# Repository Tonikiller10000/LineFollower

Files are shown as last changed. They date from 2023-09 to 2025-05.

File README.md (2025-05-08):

# LineFollower V5.0

## Description:

<table>
  <tr>
    <td>
    This is an robot made to follow a black line from start to finish for various competitions. 
    
It uses:
- ATmega328p-AU as an microcontroller(used in arduino uno);
- 16 or 20Mhz crystal resonator;
- [TB6612FNG](https://github.com/Tonikiller10000/MotorDriver_1) DC motor driver;
- [ITR8307-TR8](https://github.com/Tonikiller10000/ITR8307-TR8_SensorBar) sensor bar;
- LI-PO battery (7.2V)
- 2x DC motors with low torque high speed gear box
- robot suport (Wood, 3d printed or any low weight matherial)
    </td>
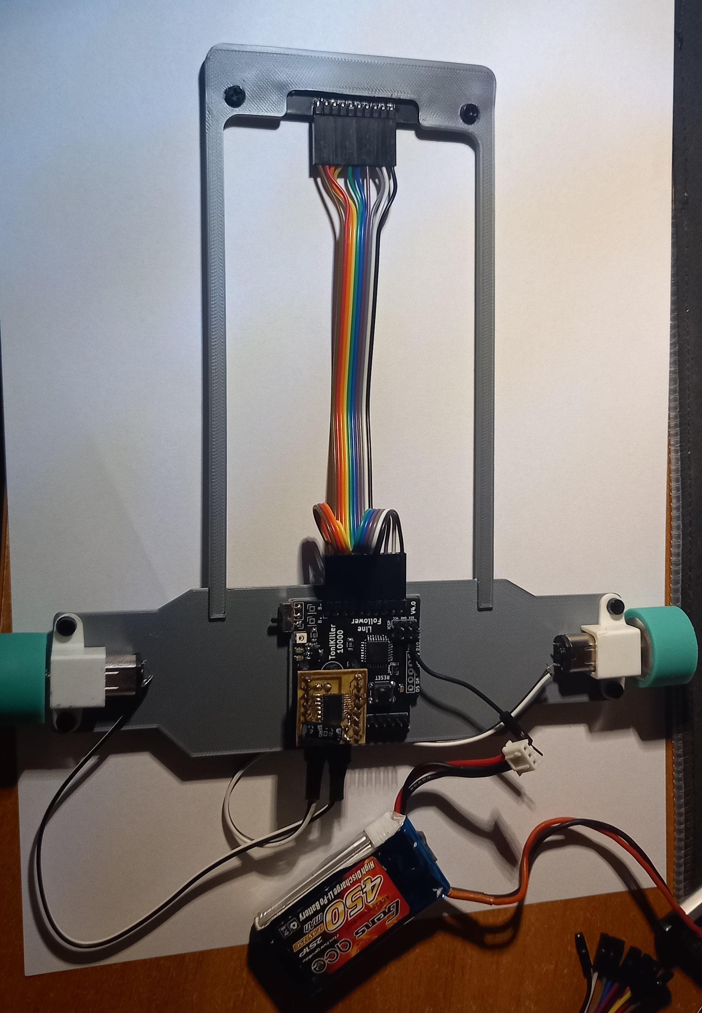
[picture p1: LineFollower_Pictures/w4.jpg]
    <td></td>
  </tr>
</table>

 ## LineFollower V5.0
<table>
  <tr>
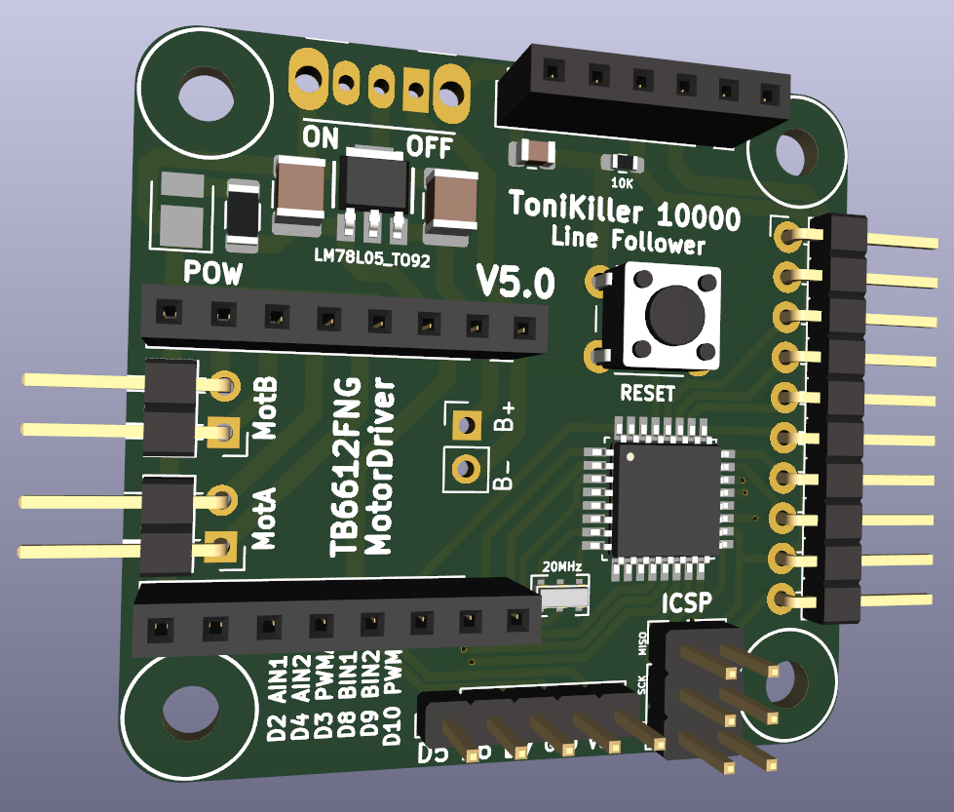
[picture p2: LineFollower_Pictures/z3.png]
    <td></td>
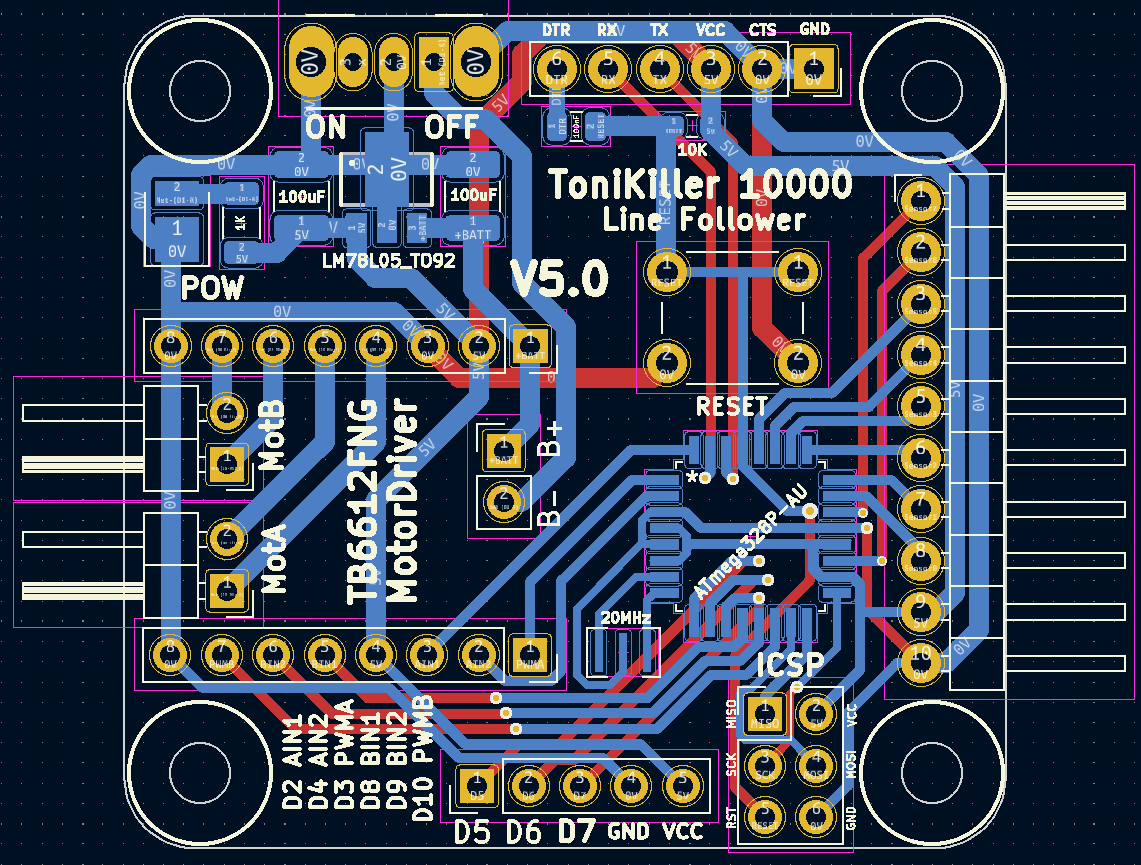
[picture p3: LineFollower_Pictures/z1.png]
    <td></td>
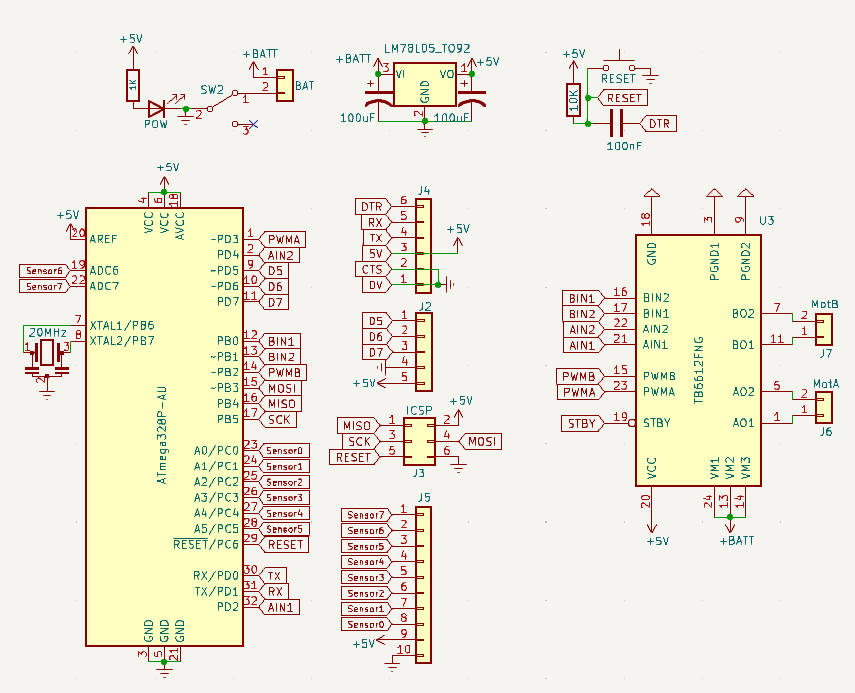
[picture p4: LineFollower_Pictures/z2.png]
    <td></td>
  </tr>
</table>

 ## LineFollower V4.0(old design)
<table>
  <tr>
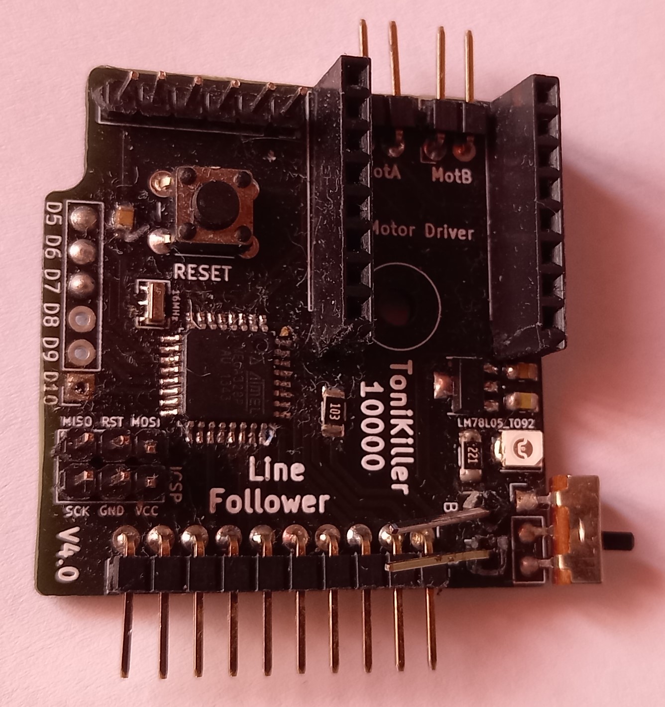
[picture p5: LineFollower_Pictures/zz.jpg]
    <td></td>
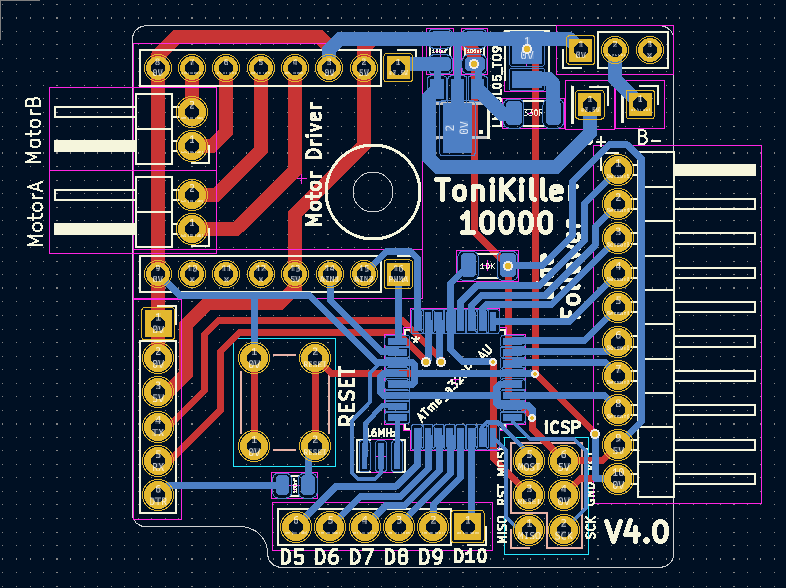
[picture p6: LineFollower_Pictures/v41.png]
    <td></td>
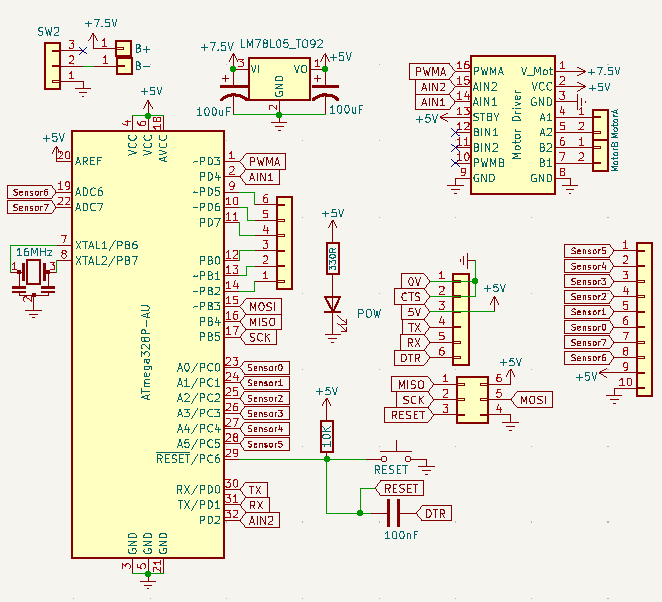
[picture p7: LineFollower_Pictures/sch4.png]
    <td></td>
  </tr>
</table>

### How it works:
The board is like a custom arduino UNO board powered from an 7.2V Li-Po battery trouth an 5V voltage regulator. The 8 analog pins are used as inputs from the sensor bar and 6 digital pins are used for the TB6612FNG motor driver witch is powered dirrectly from the battery to give more power to the motors. The reset pin has a 10K pullup resistor witch is pulled down by the reset button when it is pressed. The UART and ICSP pins wore pulled out to program the code and the bootloader of the IC.

### Programming:
[Programming of the robot](https://github.com/Tonikiller10000/LineFollower/blob/main/LineFollower_Pictures/w6.jpg): is done via UART protocoll with an [FTDI](https://github.com/Tonikiller10000/CH340G-FTDI-PROGRAMER) programming board. The code for the LineFollower is not ready. It uses the PID algorithm, and further documentation about this algorithm and the  source code for the robot will be posted this year.

### Start remote:

Robochalange remote:
[Start switch website](https://p1r.se/startmodule/)
[Start switch github](https://github.com/p1rse/robot-sumo-start-module/)
[IR Receiver Diode - TSOP38238](https://www.sparkfun.com/products/10266)
[schematic1](https://blogger.googleusercontent.com/img/b/R29vZ2xl/AVvXsEgnkNo1QEsxSPMNj7rN0opPGzlpkEMgxas9PnXUh-xvVR3l7UK27BbSvRroJmsxzwf3StBiDH0k4m-aEXX_4qJKeG5T4bKsfCBbcjgoykJY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)
[schematic2](https://blogger.googleusercontent.com/img/b/R29vZ2xl/AVvXsEjLlN9CDAmP0rq2BlWM0Xdsypyy7NfGZpMYkufZPUAMmgCRdU-KhBC8AvPr7iOOQAwod2Hw66K_vuib1FNqDIHNemtnMvlSue2krN2hfp39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)
[Q&A](https://robochallenge.ro/faq)
[MORE](https://destroyer3000.blogspot.com/2013/03/start-module-implement-yourself.html)

### How PID control work/`s

[Here](https://www.youtube.com/playlist?list=PLn8PRpmsu08pQBgjxYFXSsODEF3Jqmm-y) you can learn more about PID and under this you can see 
an analog linefollower project with and without PID:
- https://www.nutsvolts.com/magazine/article/the_pid_controller_part_1
- https://www.ecircuitcenter.com/Circuits/op_pid/op_pid.htm
- https://control.com/textbook/closed-loop-control/analog-electronic-pid-controllers/
- https://www.youtube.com/watch?v=4Y7zG48uHRo&list=PLOSOqCeZCHL0Qxb6YyrvGzjCg9FLfzHYJ

### ///////////////////////////////
- Small linefollower with op amp:https://www.youtube.com/watch?v=zZmvL0TkllI&list=WL&index=15&t=25s

### Design and mentions
[Robot support design considerations](https://github.com/Tonikiller10000/LineFollower/blob/main/LineFollower_Pictures/w3.png):
- to reach lower inertia, the components and the most of the mass of the robot should be placed on it\`s back;
- to reach a longer allowed response time from the sensor line detection to the mottor speed change it should be builted longer;
- to reach better torque on the wheels, it should be wider. 
- to mount the motors use molderd plastic motor holders, or be carefull when printing [it](https://github.com/Tonikiller10000/LineFollower/blob/main/LineFollower_Pictures/w1.jpg). 
- the case was made with autodesk fusion 360 at the 3d printer and with some M3 screws.

The next version will have the motor driver soldered on the board and motors screwed dirrectly to it as the suport. 
Another version will have a turbine for better torque and faster speeds.

## Links: 
- ATmega328p-AU (microcontroller): 
- LM78L05 (5V voltage regulator):
- Proof of work: https://github.com/Tonikiller10000/LineFollower/blob/main/LineFollower_Pictures/w2.mp4

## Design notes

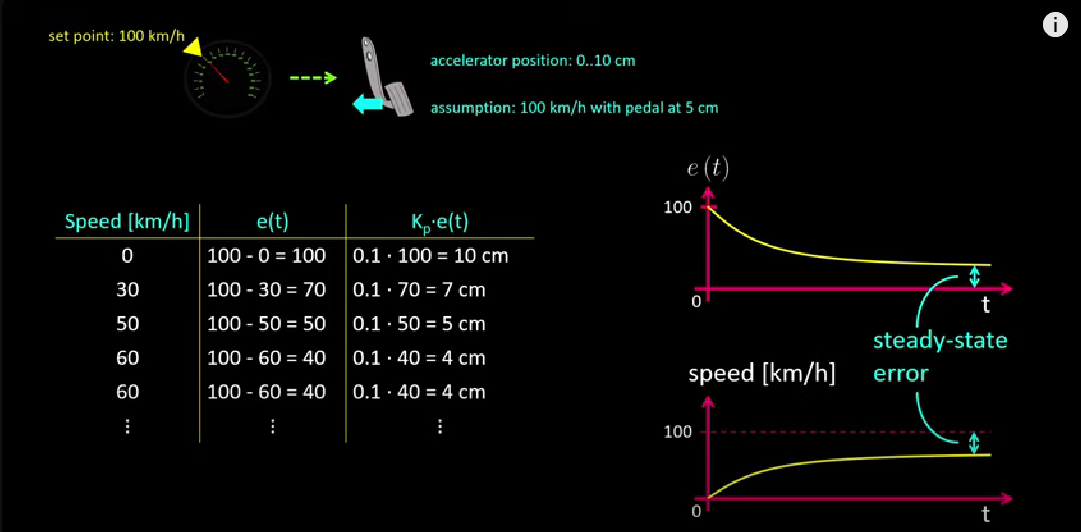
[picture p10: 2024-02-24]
PID SOFT ROBOT/Screenshot 2023-11-08 183037.png

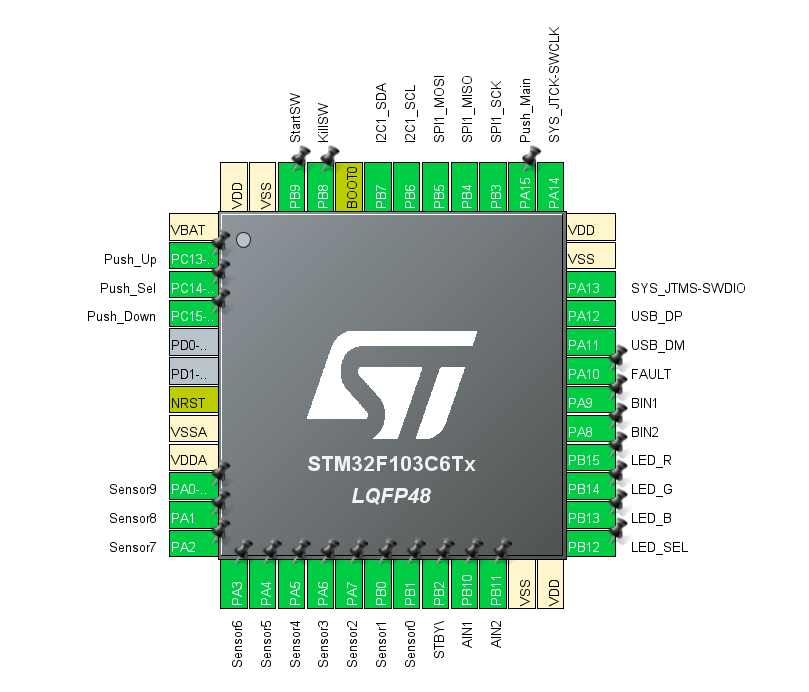
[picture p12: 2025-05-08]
LineFollower_Pictures/V6/LineFollower (17).png

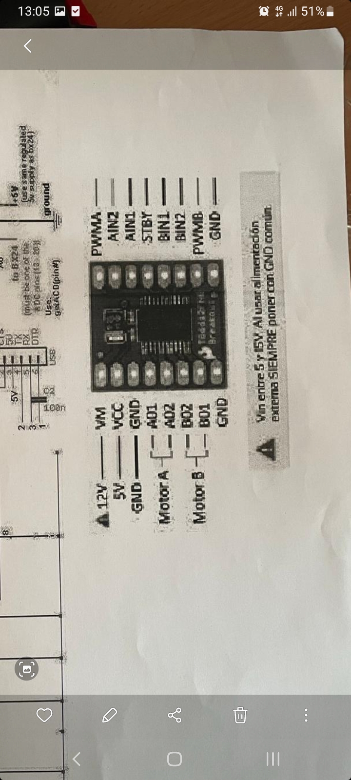
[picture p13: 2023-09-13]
LineFollower_Pictures/Screenshot_20230825-130534_Gallery.jpg

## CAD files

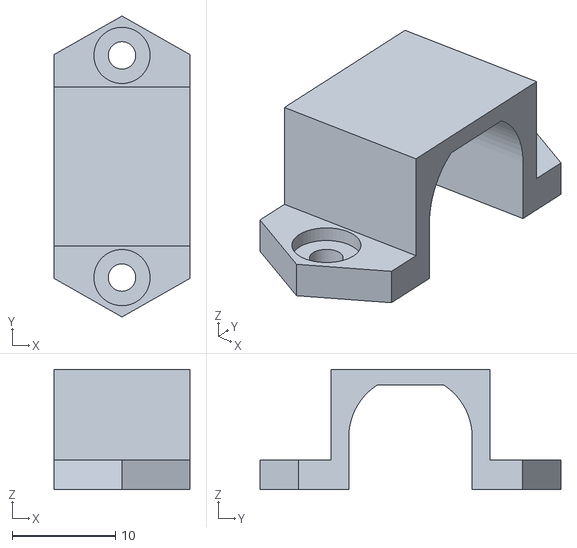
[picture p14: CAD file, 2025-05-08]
LineFollower_V6.0/n20_fixation.STL
13.1 x 29.1 x 11.6

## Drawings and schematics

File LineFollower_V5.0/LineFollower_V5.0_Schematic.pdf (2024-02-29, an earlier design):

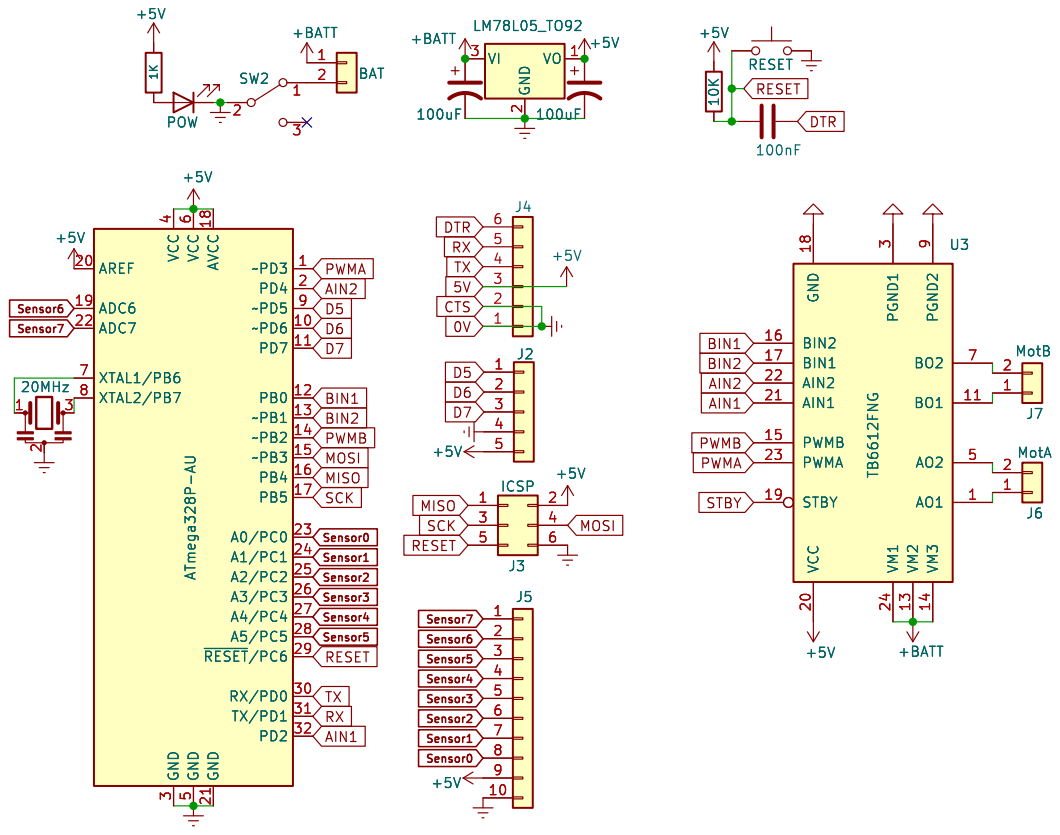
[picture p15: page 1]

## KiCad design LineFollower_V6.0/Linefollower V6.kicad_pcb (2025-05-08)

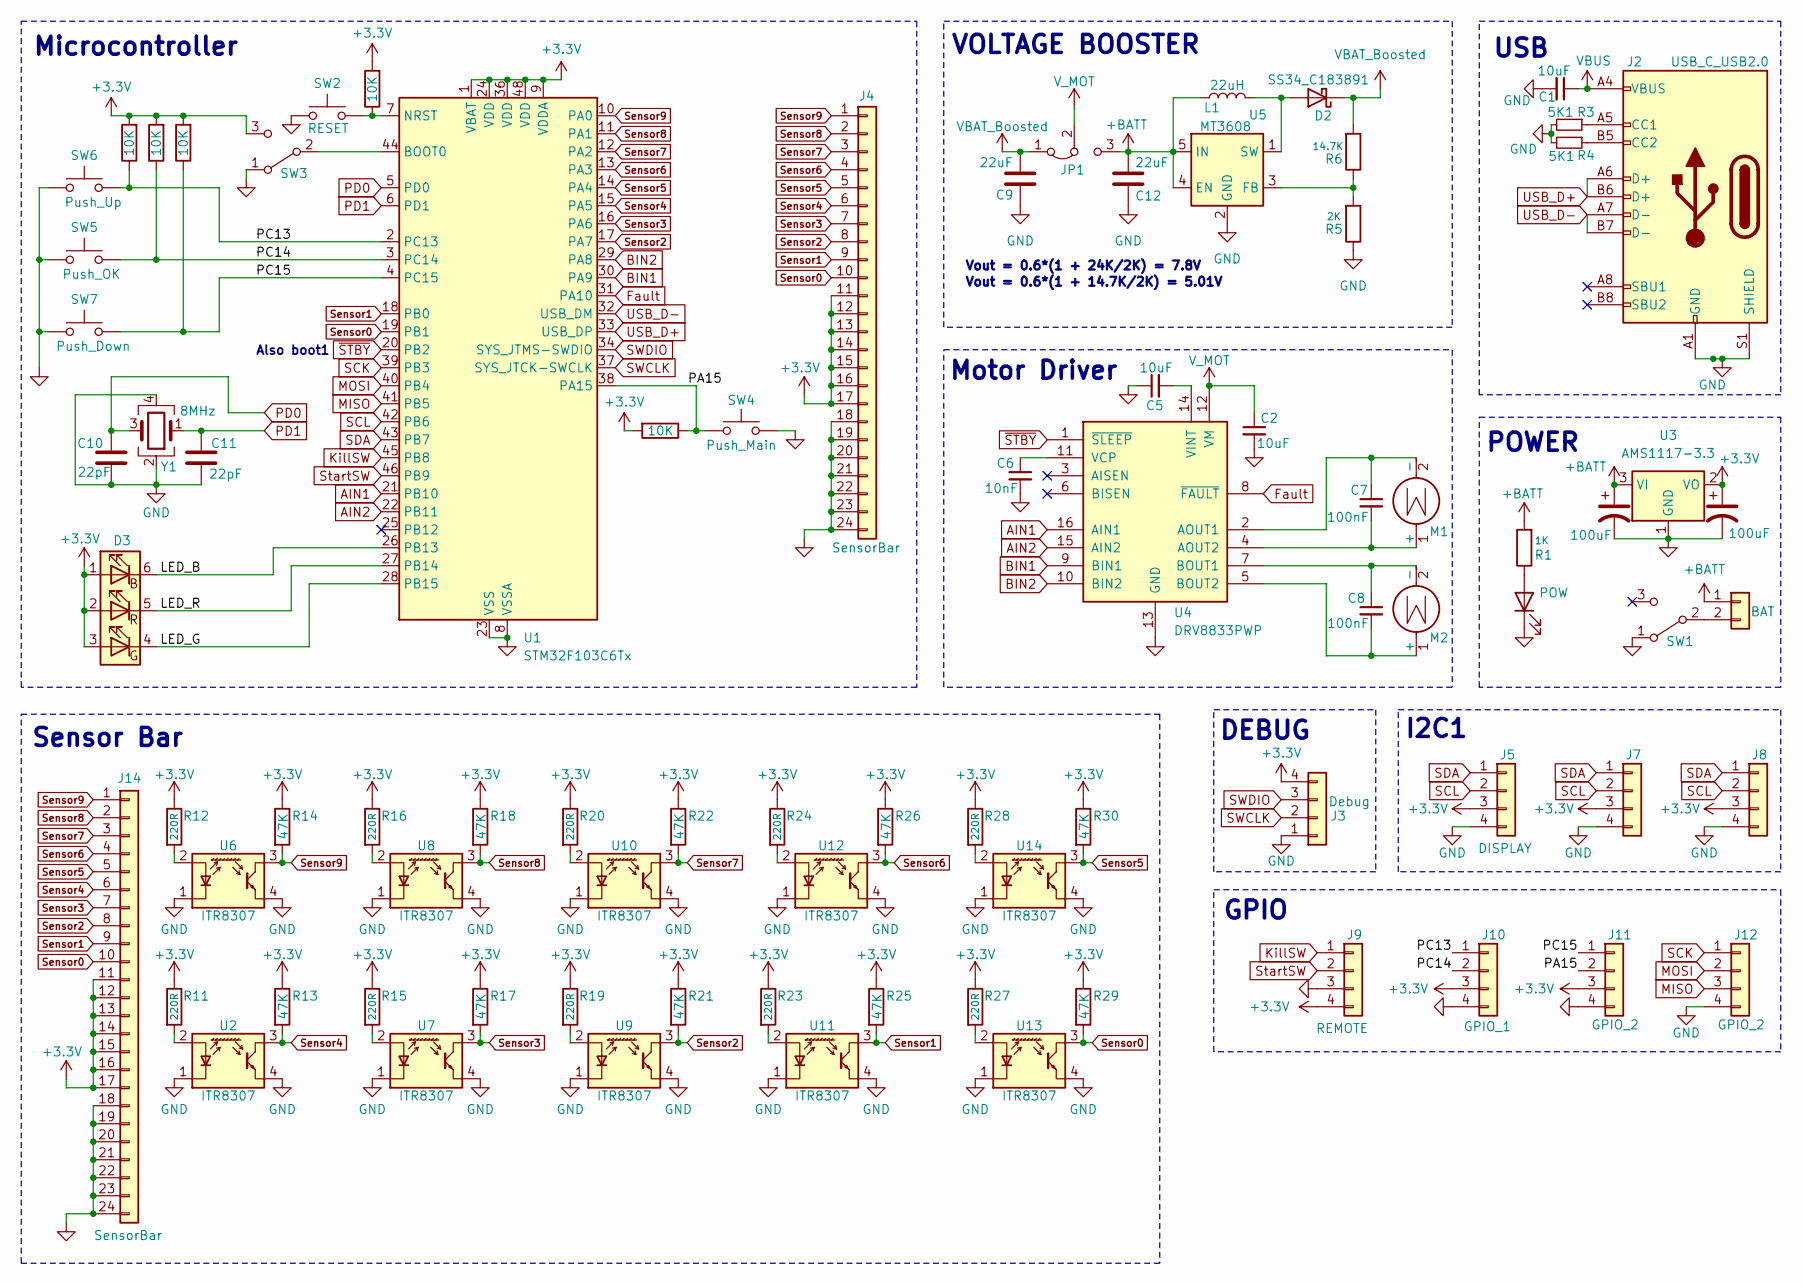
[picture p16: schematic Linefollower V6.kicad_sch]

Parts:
C1, C2, C5: 10uF; C_0603_1608Metric
C3, C4: 100uF; C_1210_3225Metric_Pad1.33x2.70mm_HandSolder
C6: 10nF; C_0603_1608Metric
C7, C8: 100nF; C_0603_1608Metric
C9, C12: 22uF
C10, C11: 22pF
D1: POW
D2: SS34_C183891
D3: SMLVN6RGB; LED_ROHM_SMLVN6
J1: BAT; PinHeader_1x02_P2.54mm_Vertical
J2: USB_C_USB2.0
J3: Debug; PinHeader_1x04_P2.54mm_Horizontal
J4, J14: SensorBar
J5, J7, J8: DISPLAY; PinHeader_1x04_P2.54mm_Vertical
J9: REMOTE; PinHeader_1x04_P2.54mm_Vertical
J10: GPIO_1; PinHeader_1x04_P2.54mm_Vertical
J11, J12: GPIO_2; PinHeader_1x04_P2.54mm_Vertical
JP1: Jumper_3_Bridged12
L1: 22uH; L_7.3x7.3_H4.5
M1, M2: Motor_DC; PinHeader_1x02_P2.54mm_Vertical
R1: 1K; R_1206_3216Metric
R2, R7, R8, R9, R10: 10K; R_1206_3216Metric
R3, R4: 5K1; R_0603_1608Metric
R5: 2K; R_0805_2012Metric_Pad1.20x1.40mm_HandSolder
R6: 14.7K; R_0805_2012Metric_Pad1.20x1.40mm_HandSolder
R11, R12, R15, R16, R19, R20, R23, R24, R27, R28: 220R; R_1206_3216Metric_Pad1.30x1.75mm_HandSolder
R13, R14, R17, R18, R21, R22, R25, R26, R29, R30: 47K; R_1206_3216Metric_Pad1.30x1.75mm_HandSolder
SW1, SW3: SW_SPDT
SW2: RESET
SW4: Push_Main
SW5: Push_OK
SW6: Push_Up
SW7: Push_Down
U1: STM32F103C6Tx; LQFP-48_7x7mm_P0.5mm
U2, U6, U7, U8, U9, U10, U11, U12, U13, U14: ITR8307; Everlight_ITR8307
U3: AMS1117-3.3; SOT-223-3_TabPin2
U4: DRV8833PWP; HTSSOP-16-1EP_4.4x5mm_P0.65mm_EP3.4x5mm_Mask2.46x2.31mm_The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
U5: MT3608; SOT-23-6
Y1: 8MHz

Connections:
+3.3V: C4.1, D3.1 (BA), D3.2 (RA), D3.3 (GA), J3.4, J4.11, J4.12, J4.13, J4.14, J4.15, J4.16, J4.17, J5.3, J7.3, J8.3, J9.4, J10.3, J11.3, J14.11, J14.12, J14.13, J14.14, J14.15, J14.16, J14.17, R2.2, R7.2, R8.2, R9.2, R10.2, R11.1, R12.1, R13.1, R14.1, R15.1, R16.1, R17.1, R18.1, R19.1, R20.1, R21.1, R22.1, R23.1, R24.1, R25.1, R26.1, R27.1, R28.1, R29.1, R30.1, SW3.3 (C), U1.1 (VBAT), U1.9 (VDDA), U1.24 (VDD), U1.36 (VDD), U1.48 (VDD), U3.2 (VO)
+BATT: C3.1, C12.1, J1.1, JP1.3 (B), L1.1, R1.2, U3.3 (VI), U5.4 (EN), U5.5 (IN)
/LED_B: D3.6 (BK), U1.26 (PB13)
/LED_G: D3.4 (GK), U1.28 (PB15)
/LED_R: D3.5 (RK), U1.27 (PB14)
/PA15: J11.2, R10.1, SW4.1, U1.38 (PA15)
/PC13: J10.1, R7.1, SW6.2, U1.2 (PC13)
/PC14: J10.2, R8.1, SW5.2, U1.3 (PC14)
/PC15: J11.1, R9.1, SW7.2, U1.4 (PC15)
AIN1: U1.21 (PB10), U4.16 (AIN1)
AIN2: U1.22 (PB11), U4.15 (AIN2)
BIN1: U1.30 (PA9), U4.9 (BIN1)
BIN2: U1.29 (PA8), U4.10 (BIN2)
Fault: U1.31 (PA10), U4.8 (~FAULT)
GND: C1.2, C2.2, C3.2, C4.2, C5.1, C6.2, C9.1, C10.1, C11.1, C12.2, D1.1 (K), J2.A1 (GND), J2.B1 (GND), J2.S1 (SHIELD), J3.1, J4.18, J4.19, J4.20, J4.21, J4.22, J4.23, J4.24, J5.4, J7.4, J8.4, J9.3, J10.4, J11.4, J12.4, J14.18, J14.19, J14.20, J14.21, J14.22, J14.23, J14.24, R3.2, R4.2, R5.1, SW1.1 (A), SW2.2, SW3.1 (A), SW4.2, SW5.1, SW6.1, SW7.1, U1.8 (VSSA), U1.23 (VSS), U1.35 (VSS), U1.47 (VSS), U2.1 (K), U2.4 (E), U3.1 (GND), U4.13 (GND), U4.17 (GND), U5.2 (GND), U6.1 (K), U6.4 (E), U7.1 (K), U7.4 (E), U8.1 (K), U8.4 (E), U9.1 (K), U9.4 (E), U10.1 (K), U10.4 (E), U11.1 (K), U11.4 (E), U12.1 (K), U12.4 (E), U13.1 (K), U13.4 (E), U14.1 (K), U14.4 (E), Y1.2, Y1.4; also elsewhere on the board
KillSW: J9.1, U1.45 (PB8)
MISO: J12.3, U1.41 (PB5)
MOSI: J12.2, U1.40 (PB4)
unnamed: D1.2 (A), R1.1
unnamed: D2.2 (A), L1.2, U5.1 (SW)
unnamed: J1.2, SW1.2 (B)
unnamed: J2.A5 (CC1), R3.1
unnamed: J2.B5 (CC2), R4.1
unnamed: C7.2, M1.1 (+), U4.4 (AOUT2)
unnamed: C7.1, M1.2 (-), U4.2 (AOUT1)
unnamed: C8.2, M2.1 (+), U4.5 (BOUT2)
unnamed: C8.1, M2.2 (-), U4.7 (BOUT1)
unnamed: SW3.2 (B), U1.44 (BOOT0)
unnamed: R2.1, SW2.1, U1.7 (NRST)
unnamed: R11.2, U2.2 (A)
unnamed: C6.1, U4.11 (VCP)
unnamed: C5.2, U4.14 (VINT)
unnamed: R5.2, R6.1, U5.3 (FB)
unnamed: R12.2, U6.2 (A)
unnamed: R15.2, U7.2 (A)
unnamed: R16.2, U8.2 (A)
unnamed: R19.2, U9.2 (A)
unnamed: R20.2, U10.2 (A)
unnamed: R23.2, U11.2 (A)
unnamed: R24.2, U12.2 (A)
unnamed: R27.2, U13.2 (A)
unnamed: R28.2, U14.2 (A)
PD0: C10.2, U1.5 (PD0), Y1.3; also elsewhere on the board
PD1: C11.2, U1.6 (PD1), Y1.1; also elsewhere on the board
SCK: J12.1, U1.39 (PB3)
SCL: J5.2, J7.2, J8.2, U1.42 (PB6)
SDA: J5.1, J7.1, J8.1, U1.43 (PB7)
SWCLK: J3.2, U1.37 (SYS_JTCK-SWCLK)
SWDIO: J3.3, U1.34 (SYS_JTMS-SWDIO)
Sensor0: J4.10, J14.10, R29.2, U1.19 (PB1), U13.3 (C)
Sensor1: J4.9, J14.9, R25.2, U1.18 (PB0), U11.3 (C)
Sensor2: J4.8, J14.8, R21.2, U1.17 (PA7), U9.3 (C)
Sensor3: J4.7, J14.7, R17.2, U1.16 (PA6), U7.3 (C)
Sensor4: J4.6, J14.6, R13.2, U1.15 (PA5), U2.3 (C)
Sensor5: J4.5, J14.5, R30.2, U1.14 (PA4), U14.3 (C)
Sensor6: J4.4, J14.4, R26.2, U1.13 (PA3), U12.3 (C)
Sensor7: J4.3, J14.3, R22.2, U1.12 (PA2), U10.3 (C)
Sensor8: J4.2, J14.2, R18.2, U1.11 (PA1), U8.3 (C)
Sensor9: J4.1, J14.1, R14.2, U1.10 (PA0), U6.3 (C)
StartSW: J9.2, U1.46 (PB9)
USB_D+: J2.A6 (D+), J2.B6 (D+), U1.33 (USB_DP)
USB_D-: J2.A7 (D-), J2.B7 (D-), U1.32 (USB_DM)
VBAT_Boosted: C9.2, D2.1 (K), JP1.1 (A), R6.2
VBUS: C1.1, J2.A4 (VBUS)
V_MOT: C2.1, JP1.2 (C), U4.12 (VM)
~STBY: U1.20 (PB2), U4.1 (~SLEEP)

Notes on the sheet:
Motor Driver
Also boot1
Vout = 0.6*(1 + 24K/2K) = 7.8V
POWER
Sensor Bar
Microcontroller
I2C1
USB
VOLTAGE BOOSTER
GPIO
Vout = 0.6*(1 + 14.7K/2K) = 5.01V
DEBUG

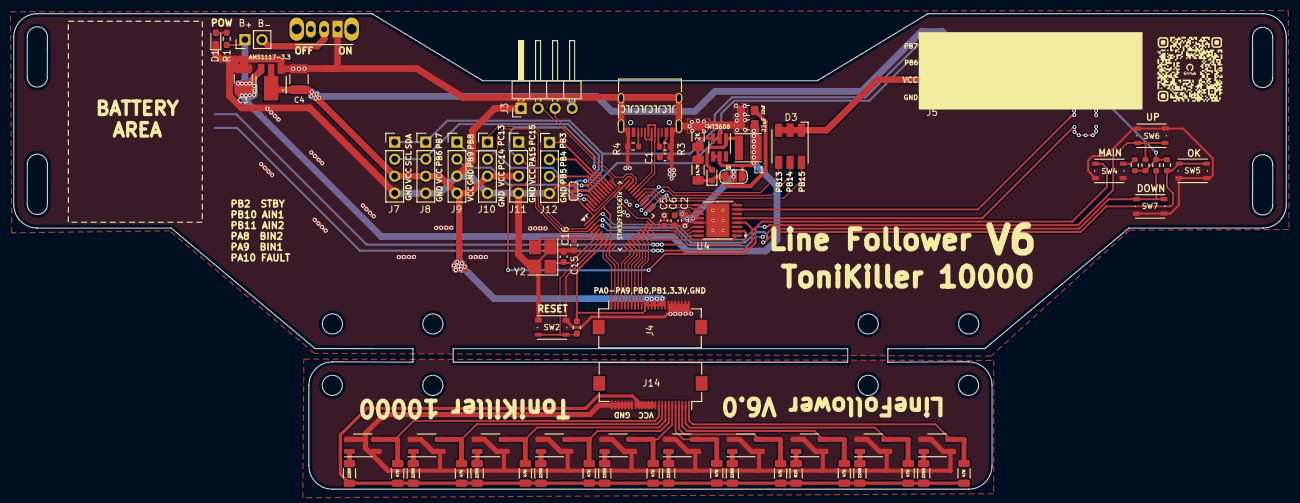
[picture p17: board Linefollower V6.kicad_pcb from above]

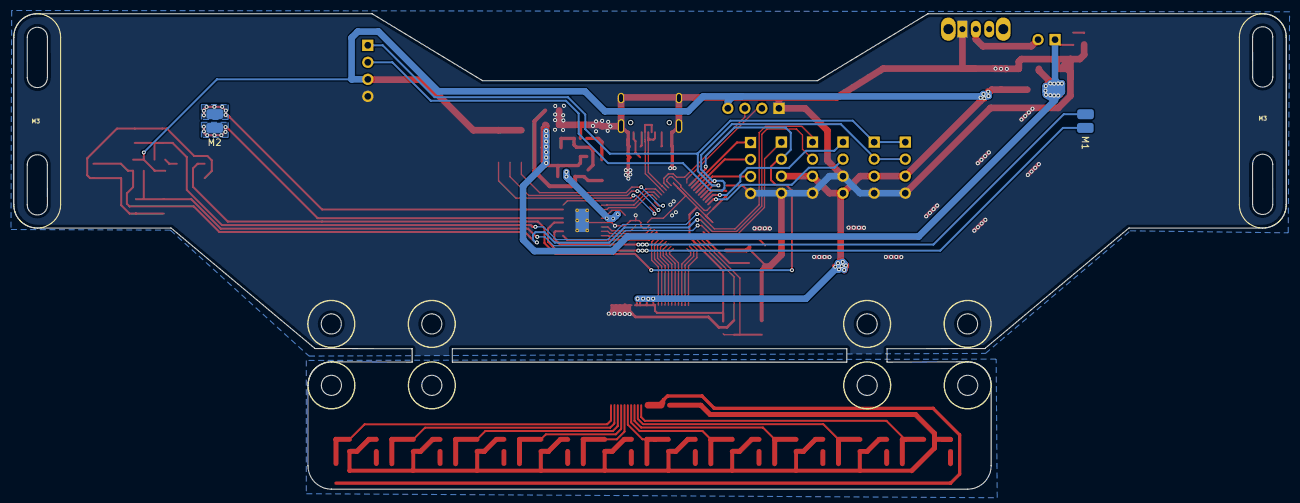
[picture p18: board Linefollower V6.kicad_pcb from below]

Board: 2 copper layers, 190.0 x 71.0 mm, 81 parts (2 on the bottom side), 66 nets.

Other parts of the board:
C15, C16: 22pF; C_0603_1608Metric
Y2: 8MHz; Crystal_SMD_3225-4Pin_3.2x2.5mm_HandSoldering

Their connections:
GND: C15.1, C16.1, Y2.2, Y2.4; also elsewhere on the board
PD0: C15.2, Y2.3; also elsewhere on the board
PD1: C16.2, Y2.1; also elsewhere on the board

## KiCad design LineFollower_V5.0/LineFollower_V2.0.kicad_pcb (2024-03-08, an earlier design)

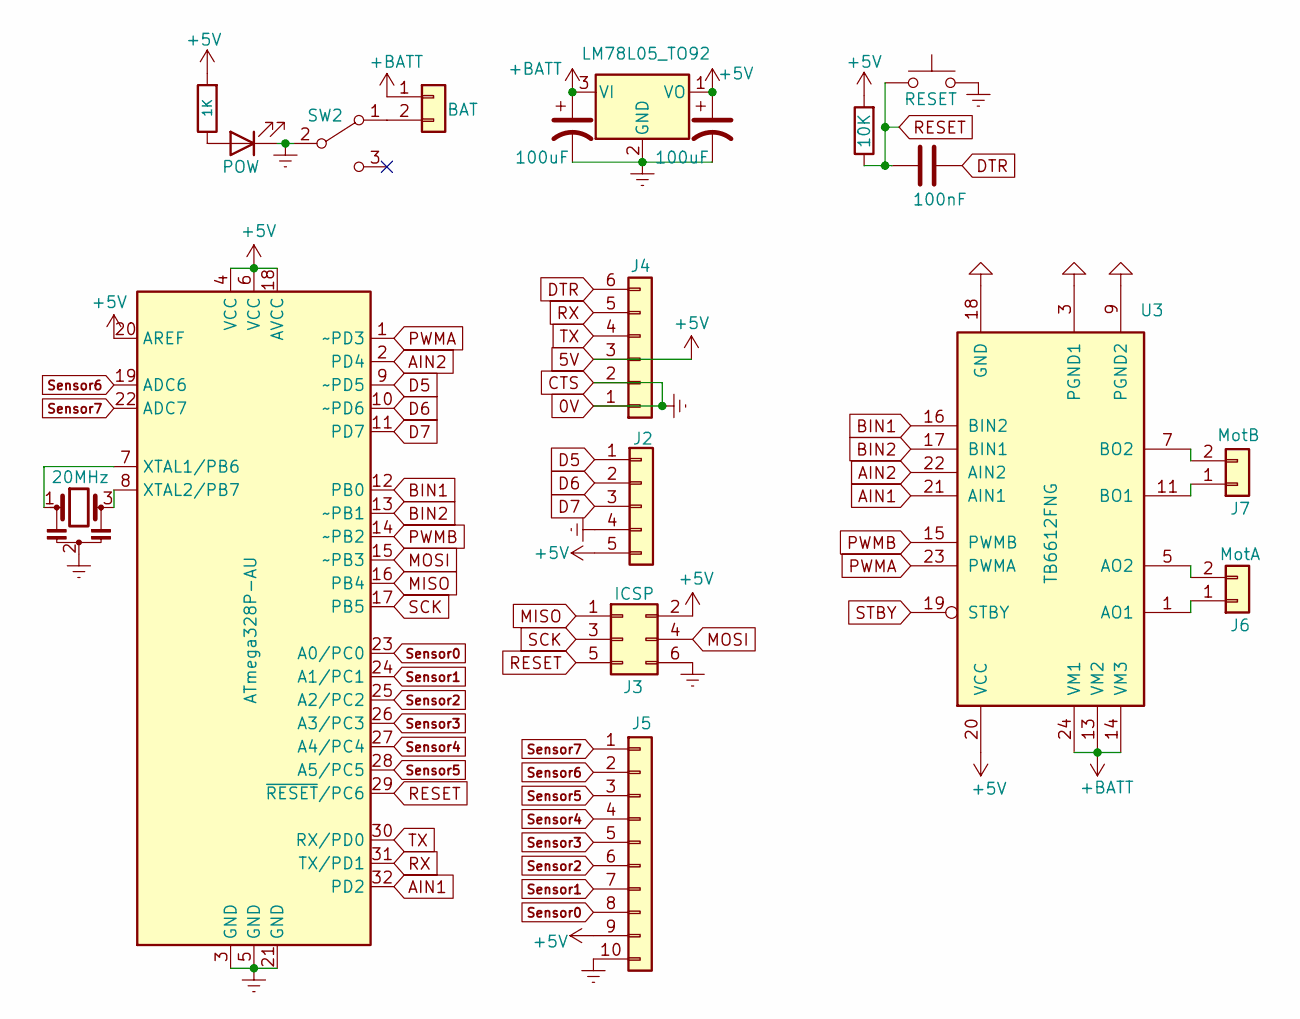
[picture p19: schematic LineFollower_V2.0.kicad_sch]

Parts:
C2, C3: 100uF; C_1210_3225Metric_Pad1.33x2.70mm_HandSolder
C6: 100nF; C_0805_2012Metric
D1: POW
J1: BAT; PinHeader_1x02_P2.54mm_Vertical
J2: Conn_01x05
J3: ICSP; PinHeader_2x03_P2.54mm_Vertical
J4: Conn_01x06_MountingPin
J5: Conn_01x10; PinHeader_1x10_P2.54mm_Horizontal
J6: MotA; PinHeader_1x02_P2.54mm_Vertical
J7: MotB; PinHeader_1x02_P2.54mm_Vertical
R1: 10K; R_1206_3216Metric
R2: 1K; R_1206_3216Metric
SW1: RESET
SW2: SW_SPDT
U1: ATmega328P-AU; TQFP-32_7x7mm_P0.8mm
U2: LM78L05_TO92; TO-92_Inline
U3: TB6612FNG; SSOP-24_5.3x8.2mm_P0.65mm
Y1: 20MHz; Resonator_SMD_Murata_CSTxExxV-3Pin_3.0x1.1mm

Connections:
0V: C2.2, C3.2, D1.1 (K), J2.4, J3.6, J4.1, J4.2, J5.10, SW1.2, SW2.2 (B), U1.3 (GND), U1.5 (GND), U1.21 (GND), U2.2 (GND), Y1.2; also elsewhere on the board
5V: C3.1, J2.5, J3.2, J4.3, J5.9, R1.2, R2.2, U1.4 (VCC), U1.6 (VCC), U1.18 (AVCC), U1.20 (AREF), U2.1 (VO), U3.20 (VCC); also elsewhere on the board
+BATT: C2.1, J1.1, U2.3 (VI), U3.13 (VM2), U3.14 (VM3), U3.24 (VM1); also elsewhere on the board
AIN1: U1.32 (PD2), U3.21 (AIN1); also elsewhere on the board
AIN2: U1.2 (PD4), U3.22 (AIN2); also elsewhere on the board
BIN1: U1.12 (PB0), U3.16 (BIN2); also elsewhere on the board
BIN2: U1.13 (~PB1), U3.17 (BIN1); also elsewhere on the board
D5: J2.1, U1.9 (~PD5)
D6: J2.2, U1.10 (~PD6)
D7: J2.3, U1.11 (PD7)
DTR: C6.1, J4.6
MISO: J3.1, U1.16 (PB4)
MOSI: J3.4, U1.15 (~PB3)
unnamed: D1.2 (A), R2.1
unnamed: J1.2, SW2.1 (A)
unnamed 15: J6.1, U3.1 (AO1), U3.2 (AO1); also elsewhere on the board
unnamed 16: J6.2, U3.5 (AO2), U3.6 (AO2); also elsewhere on the board
unnamed 17: J7.1, U3.11 (BO1), U3.12 (BO1); also elsewhere on the board
unnamed 18: J7.2, U3.7 (BO2), U3.8 (BO2); also elsewhere on the board
unnamed: U1.7 (XTAL1/PB6), Y1.1
unnamed: U1.8 (XTAL2/PB7), Y1.3
unnamed: U3.3 (PGND1), U3.4 (PGND1), U3.9 (PGND2), U3.10 (PGND2), U3.18 (GND)
PWMA: U1.1 (~PD3), U3.23 (PWMA); also elsewhere on the board
PWMB: U1.14 (~PB2), U3.15 (PWMB); also elsewhere on the board
RESET: C6.2, J3.5, R1.1, SW1.1, U1.29 (~RESET/PC6)
RX: J4.5, U1.31 (TX/PD1)
SCK: J3.3, U1.17 (PB5)
Sensor0: J5.8, U1.23 (A0/PC0)
Sensor1: J5.7, U1.24 (A1/PC1)
Sensor2: J5.6, U1.25 (A2/PC2)
Sensor3: J5.5, U1.26 (A3/PC3)
Sensor4: J5.4, U1.27 (A4/PC4)
Sensor5: J5.3, U1.28 (A5/PC5)
Sensor6: J5.2, U1.19 (ADC6)
Sensor7: J5.1, U1.22 (ADC7)
TX: J4.4, U1.30 (RX/PD0)

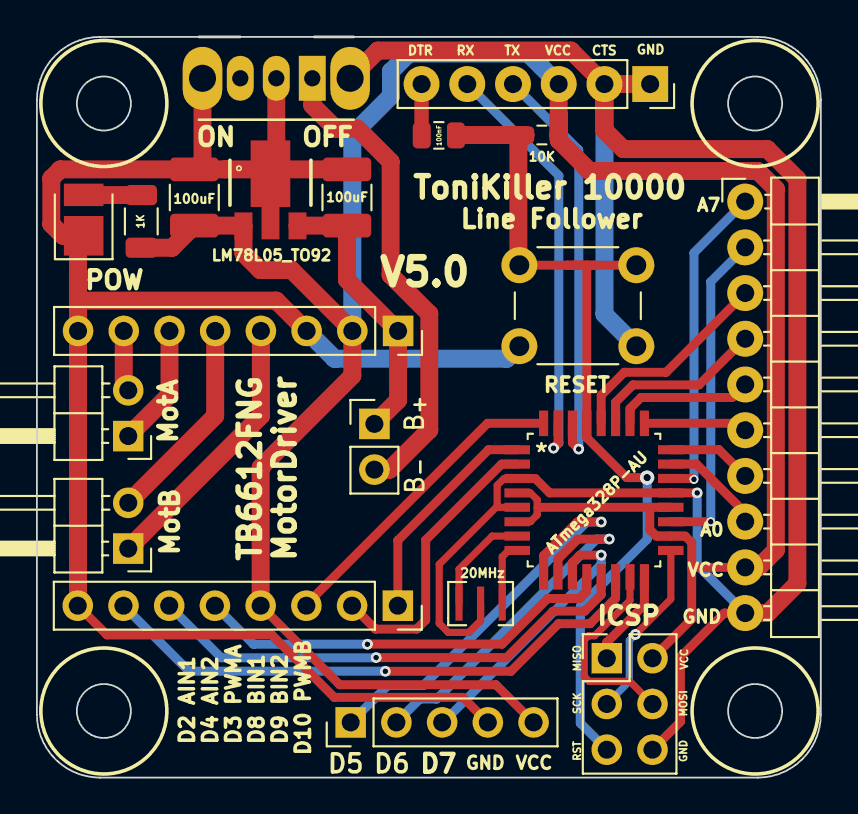
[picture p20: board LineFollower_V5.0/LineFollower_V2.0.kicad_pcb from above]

Board: 2 copper layers, 43.5 x 41.2 mm, 20 parts (0 on the bottom side), 35 nets.

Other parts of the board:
J8: BAT; PinSocket_1x08_P2.54mm_Vertical
J9: Conn_01x03; PinSocket_1x08_P2.54mm_Vertical

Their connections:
0V: J8.3, J8.8, J9.8; also elsewhere on the board
5V: J8.2, J9.4; also elsewhere on the board
+BATT: J8.1; also elsewhere on the board
AIN1: J9.3; also elsewhere on the board
AIN2: J9.2; also elsewhere on the board
BIN1: J9.5; also elsewhere on the board
BIN2: J9.6; also elsewhere on the board
unnamed 15: J8.6; also elsewhere on the board
unnamed 16: J8.7; also elsewhere on the board
unnamed 17: J8.4; also elsewhere on the board
unnamed 18: J8.5; also elsewhere on the board
PWMA: J9.1; also elsewhere on the board
PWMB: J9.7; also elsewhere on the board

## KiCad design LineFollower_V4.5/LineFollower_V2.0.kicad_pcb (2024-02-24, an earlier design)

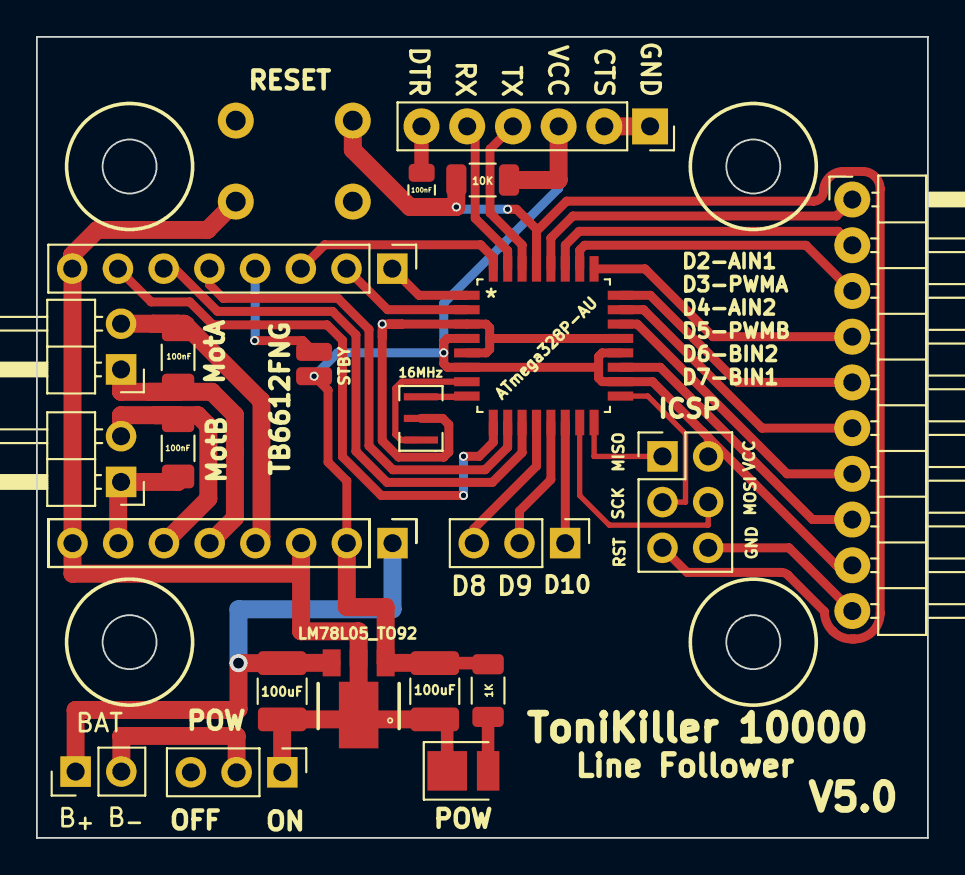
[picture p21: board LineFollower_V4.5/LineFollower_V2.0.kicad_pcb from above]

Board: 2 copper layers, 49.5 x 44.5 mm, 21 parts (1 on the bottom side), 29 nets.

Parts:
C2, C3: 100uF; C_1210_3225Metric_Pad1.33x2.70mm_HandSolder
C4, C5: 100nF; C_1206_3216Metric_Pad1.33x1.80mm_HandSolder
C6: 100nF; C_0805_2012Metric
D1: POW; LED_PLCC_2835
J1: BAT; PinHeader_1x02_P2.54mm_Vertical
J3: ICSP; PinHeader_2x03_P2.54mm_Vertical
J4: Conn_01x06_MountingPin; PinSocket_1x06_P2.54mm_Vertical
J5: Conn_01x10; PinHeader_1x10_P2.54mm_Horizontal
J6: MotA; PinHeader_1x02_P2.54mm_Horizontal
J7: MotB; PinHeader_1x02_P2.54mm_Horizontal
R1: 10K; R_1206_3216Metric
R2: 1K; R_1206_3216Metric
SW1: RESET; SW_PUSH_6mm
SW2, SW4: POW; PinHeader_1x03_P2.54mm_Vertical
U1: ATmega328P-AU; TQFP32_32A_MCH
U2: LM78L05_TO92; PK(R-PSSO-F3)
U3: TB6612FNG; MotorDriver111
Y1: 16MHz; Resonator_SMD_Murata_CSTxExxV-3Pin_3.0x1.1mm

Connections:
0V: C2.2, C3.2, D1.1 (K), J3.6, J4.1, J4.2, J5.10, SW1.1, SW2.1, U1.3 (GND), U1.5 (GND), U1.21 (GND), U2.2 (GND), U3.8 (BO2), U3.9 (PGND2), U3.14 (VM3), Y1.2
5V: C3.1, J3.2, J4.3, J5.9, R1.2, R2.2, U1.4 (VCC), U1.6 (VCC), U1.18 (AVCC), U1.20 (AREF), U2.1 (VO), U3.4 (PGND1), U3.15 (PWMB)
10: SW4.1, U1.14 (~PB2)
+BATT: C2.1, J1.1, U2.3 (VI)
BIN1: U1.11 (PD7), U3.6 (AO2), U3.16 (BIN2)
BIN2: U1.10 (~PD6), U3.5 (AO2)
D8: SW4.3, U1.12 (PB0)
D9: SW4.2, U1.13 (~PB1)
DTR: C6.1, J4.6
MISO: J3.1, U1.16 (PB4)
MOSI: J3.4, U1.15 (~PB3)
unnamed: D1.2 (A), R2.1
unnamed: J1.2, SW2.2
unnamed: U3.1 (AO1), U3.2 (AO1)
unnamed: U1.7 (XTAL1/PB6), Y1.1
unnamed: U1.8 (XTAL2/PB7), Y1.3
PWMB: U1.9 (~PD5), U3.7 (BO2)
RESET: C6.2, J3.5, R1.1, SW1.2, U1.29 (~RESET/PC6)
RX: J4.5, U1.31 (TX/PD1)
SCK: J3.3, U1.17 (PB5)
Sensor0: J5.6, U1.23 (A0/PC0)
Sensor1: J5.5, U1.24 (A1/PC1)
Sensor2: J5.4, U1.25 (A2/PC2)
Sensor3: J5.3, U1.26 (A3/PC3)
Sensor4: J5.2, U1.27 (A4/PC4)
Sensor5: J5.1, U1.28 (A5/PC5)
Sensor6: J5.8, U1.19 (ADC6)
Sensor7: J5.7, U1.22 (ADC7)
TX: J4.4, U1.30 (RX/PD0)

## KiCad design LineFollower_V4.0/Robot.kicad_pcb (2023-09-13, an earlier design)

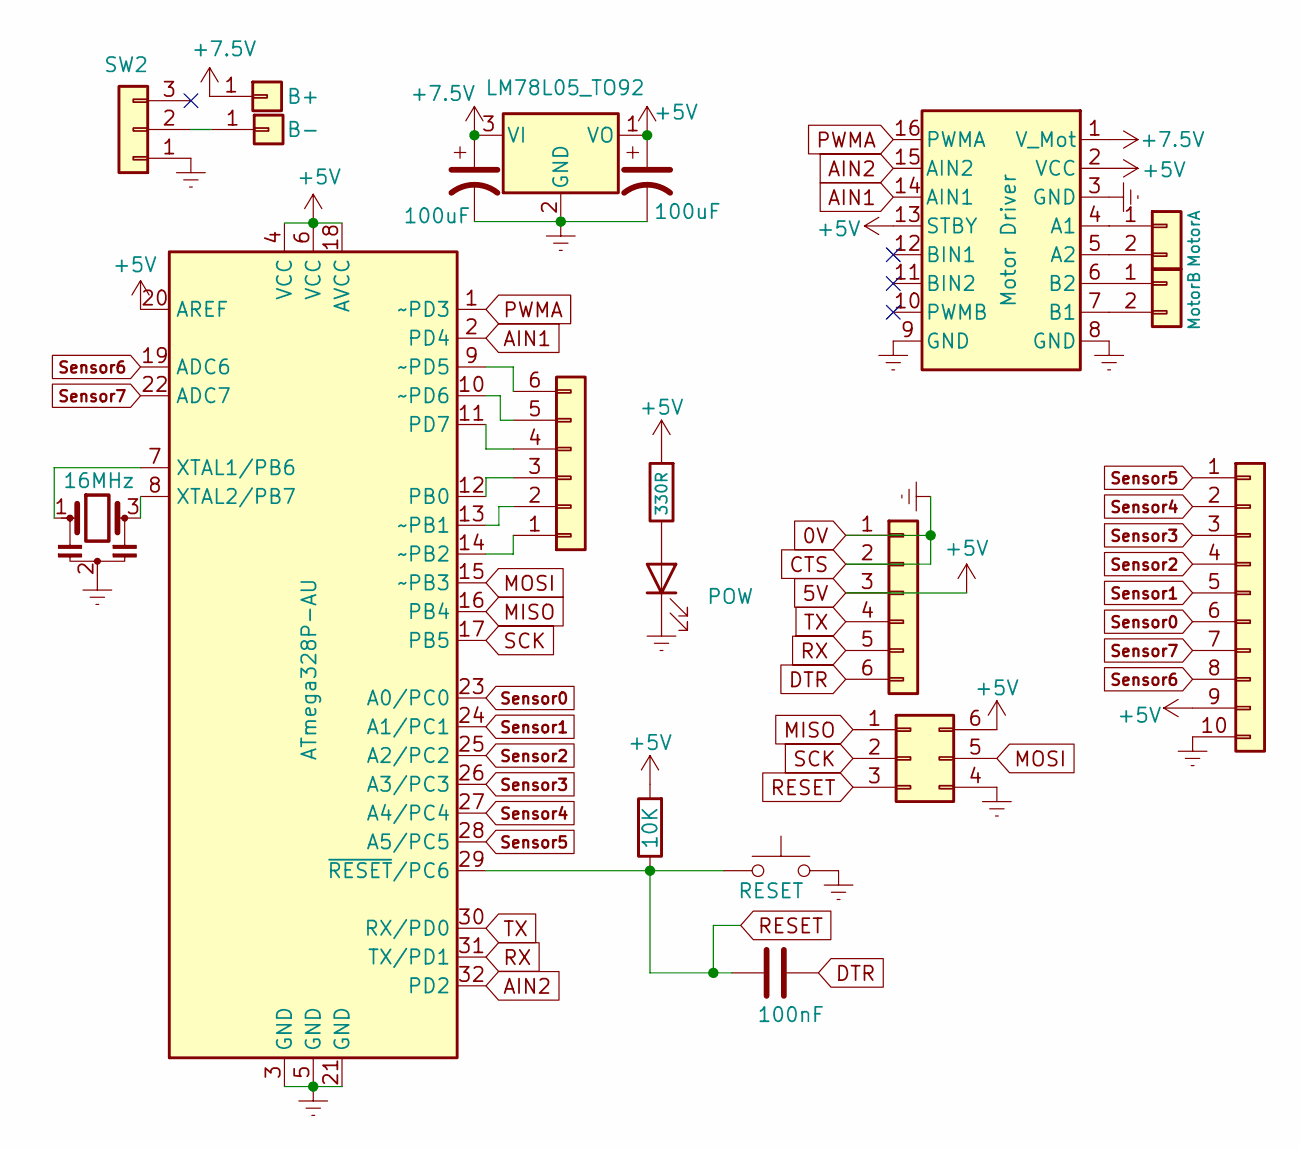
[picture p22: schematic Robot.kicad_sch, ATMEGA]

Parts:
C1, C2: 100uF
C3: 100nF
D1: POW
J1: Conn_01x06_MountingPin
J2: ICSP
J3: MotorA
J4: MotorB
J5: Conn_01x10
J6: Digital PINS
J8: B+
J9: B-
R1: 10K
R2: 330R
SW1: RESET
SW2: POW
U1: ATmega328P-AU; TQFP-32_7x7mm_P0.8mm
U2: LM78L05_TO92; TO-92_Inline
U3: Motor Driver; MotorDriver111
Y1: 16MHz

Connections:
0V: C1.2, C2.2, D1.1 (K), J1.1, J1.2, J2.4, J5.10, SW1.1, SW2.1, U1.3 (GND), U1.5 (GND), U1.21 (GND), U2.2 (GND), U3.3 (GND), U3.8 (GND), U3.9 (GND), Y1.2
5V: C2.1, J1.3, J2.6, J5.9, R1.2, R2.2, U1.4 (VCC), U1.6 (VCC), U1.18 (AVCC), U1.20 (AREF), U2.1 (VO), U3.2 (VCC), U3.13 (STBY)
+7.5V: C1.1, J8.1, U2.3 (VI), U3.1 (V_Mot)
AIN1: U1.2 (PD4), U3.14 (AIN1)
AIN2: U1.32 (PD2), U3.15 (AIN2)
DTR: C3.1, J1.6
MISO: J2.1, U1.16 (PB4)
MOSI: J2.5, U1.15 (~PB3)
unnamed: D1.2 (A), R2.1
unnamed: J3.1, U3.4 (A1)
unnamed: J3.2, U3.5 (A2)
unnamed: J4.1, U3.6 (B2)
unnamed: J4.2, U3.7 (B1)
unnamed: J9.1, SW2.2
unnamed: U1.7 (XTAL1/PB6), Y1.1
unnamed: U1.8 (XTAL2/PB7), Y1.3
unnamed: J6.6, U1.9 (~PD5)
unnamed: J6.5, U1.10 (~PD6)
unnamed: J6.4, U1.11 (PD7)
unnamed: J6.3, U1.12 (PB0)
unnamed: J6.2, U1.13 (~PB1)
unnamed: J6.1, U1.14 (~PB2)
PWMA: U1.1 (~PD3), U3.16 (PWMA)
RESET: C3.2, J2.3, R1.1, SW1.2, U1.29 (~RESET/PC6)
RX: J1.5, U1.31 (TX/PD1)
SCK: J2.2, U1.17 (PB5)
Sensor0: J5.6, U1.23 (A0/PC0)
Sensor1: J5.5, U1.24 (A1/PC1)
Sensor2: J5.4, U1.25 (A2/PC2)
Sensor3: J5.3, U1.26 (A3/PC3)
Sensor4: J5.2, U1.27 (A4/PC4)
Sensor5: J5.1, U1.28 (A5/PC5)
Sensor6: J5.8, U1.19 (ADC6)
Sensor7: J5.7, U1.22 (ADC7)
TX: J1.4, U1.30 (RX/PD0)

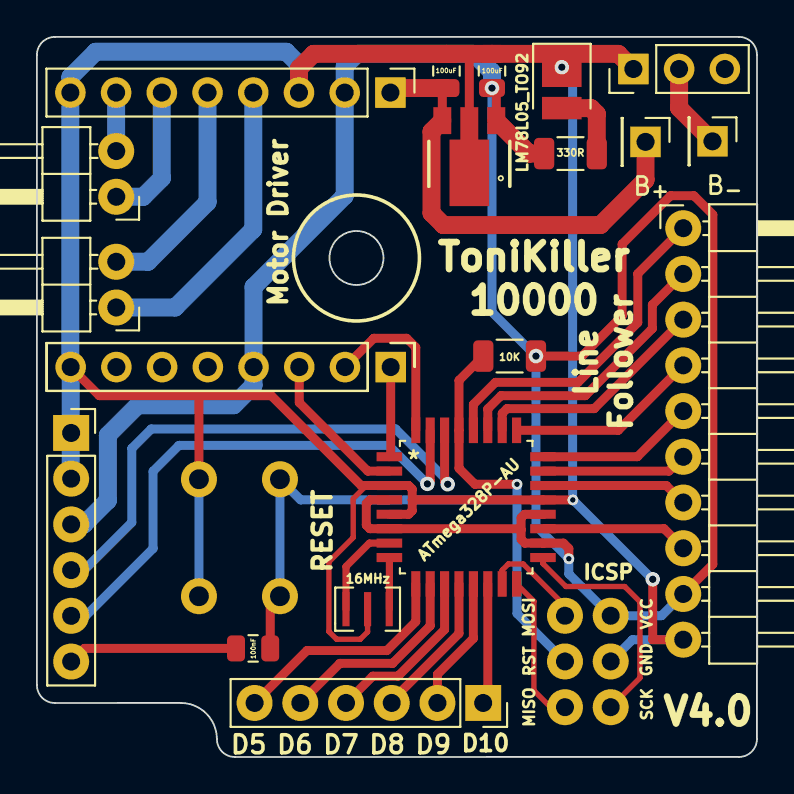
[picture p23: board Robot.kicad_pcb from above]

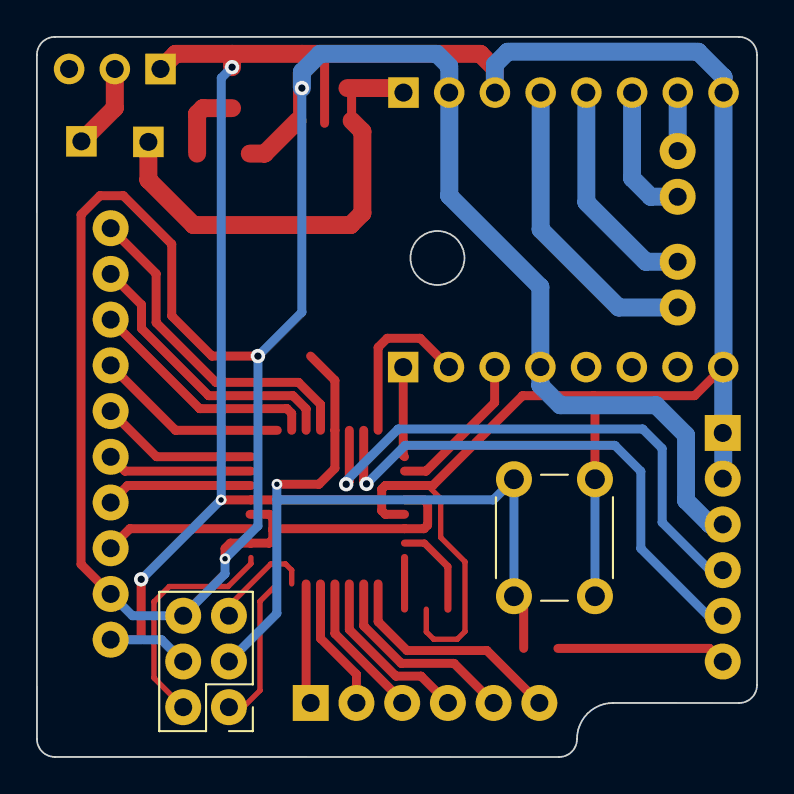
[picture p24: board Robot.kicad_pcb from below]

Board: 2 copper layers, 40.0 x 40.0 mm, 20 parts (2 on the bottom side), 35 nets.

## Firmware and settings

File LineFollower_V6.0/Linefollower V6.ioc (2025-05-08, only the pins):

Mcu.UserName=STM32F103C6Tx
PA0-WKUP.Signal=ADCx_IN0
PA1.Signal=ADCx_IN1
PA10.Signal=GPIO_Output
PA11.Signal=USB_DM
PA12.Signal=USB_DP
PA13.Signal=SYS_JTMS-SWDIO
PA14.Signal=SYS_JTCK-SWCLK
PA2.Signal=ADCx_IN2
PA3.Signal=ADCx_IN3
PA4.Signal=ADCx_IN4
PA5.Signal=ADCx_IN5
PA6.Signal=ADCx_IN6
PA7.Signal=ADCx_IN7
PA8.Signal=S_TIM1_CH1
PA9.Signal=S_TIM1_CH2
PB0.Signal=ADCx_IN8
PB1.Signal=ADCx_IN9
PB10.Signal=S_TIM2_CH3
PB11.Signal=S_TIM2_CH4
PB2.Signal=GPIO_Output
PB5.Signal=GPIO_Input
PB6.Signal=GPIO_Input
PB7.Signal=GPIO_Input

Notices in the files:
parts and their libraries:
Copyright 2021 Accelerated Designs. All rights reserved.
